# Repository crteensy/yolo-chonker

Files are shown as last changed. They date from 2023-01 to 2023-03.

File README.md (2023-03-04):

# yolo-chonker

## if you are a betaflight dev and received an assembled board from crteensy

There is a branch with the "as-built" state that you received: https://github.com/crteensy/yolo-chonker/tree/as-built-20230303

It includes a description of minor mistakes and errors, and what paste (high temp, low temp) was used where.

## What this is

betaflight developer FC for the H735

The layout has 6 layers, and the decoupling is designed for oshpark's 6-layer stackup (see oshpark_6L_stackup.png)

- Format: 30x30 hole distance
- Battery voltage range: 2-6S
- 5V DCDC: LMR33620CRNXT
- 3V3: TPS62824
- Separate DCDC for HD out; LMR33620CRNXT set for 10V or 5V, configured with a solder jumper
- MCU: STM32H735
- peripherals that can be connected to the MCU with solder jumpers:
  - IMU: ICM-20602 and BMI270; dual gyro is possible
  - Flash: S25FL064L
  - Baro: DPS310
  - LEDs:
    - voltage rails LEDs: HD DCDC (5/10 V), 5V, 3V3
    - two standard LEDs for the FC
    - WS2812B including an output pad to attach more
  - battery voltage sensing
- SWD pads
- no analog OSD
- no HD connector

CC-BY-SA-4.0
https://creativecommons.org/licenses/by-sa/4.0/legalcode

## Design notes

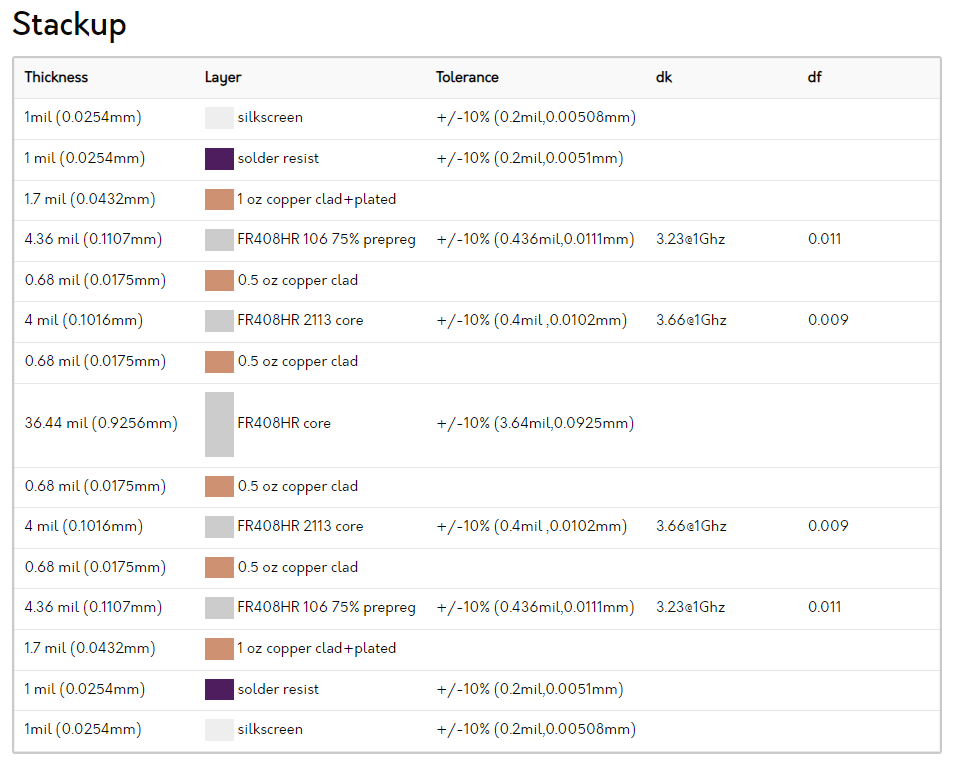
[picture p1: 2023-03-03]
oshpark_6L_stackup.png

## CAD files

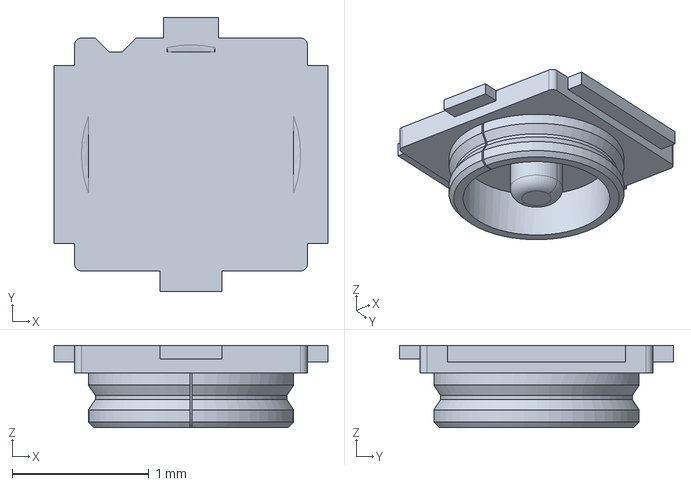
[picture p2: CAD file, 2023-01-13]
3D/A-4JA.stp
2.00 x 2.00 x 0.6 mm

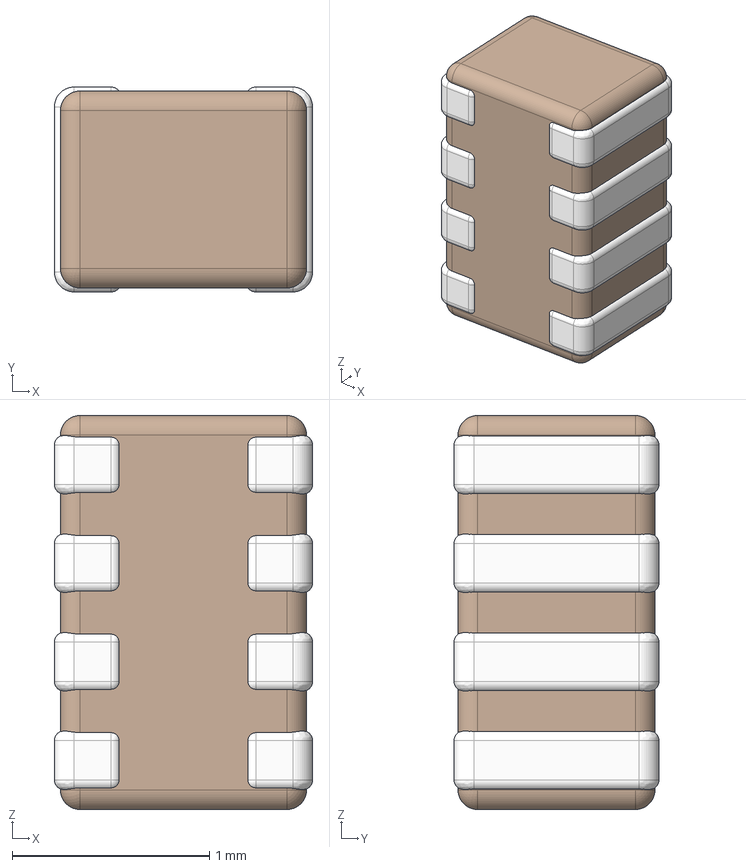
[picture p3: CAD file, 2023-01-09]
3D/idc.stp
1.31 x 1.04 x 2.00 mm

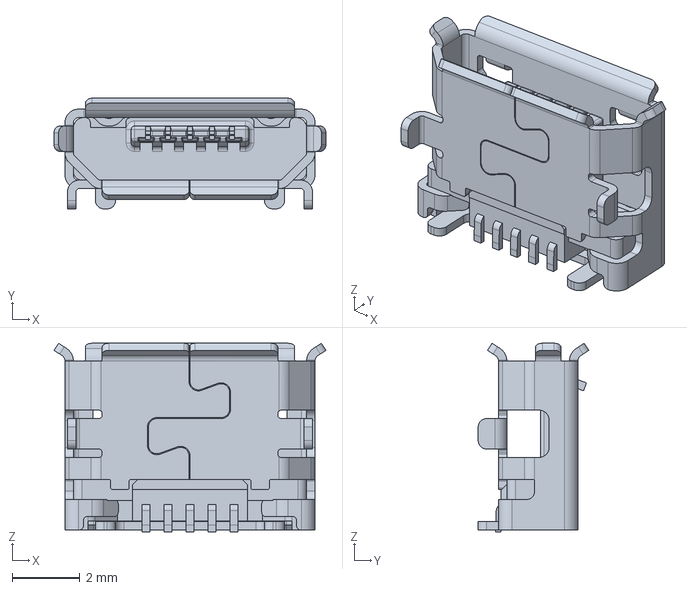
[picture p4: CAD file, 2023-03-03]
3D/10118194c.stp
8.05 x 3.27 x 5.58 mm

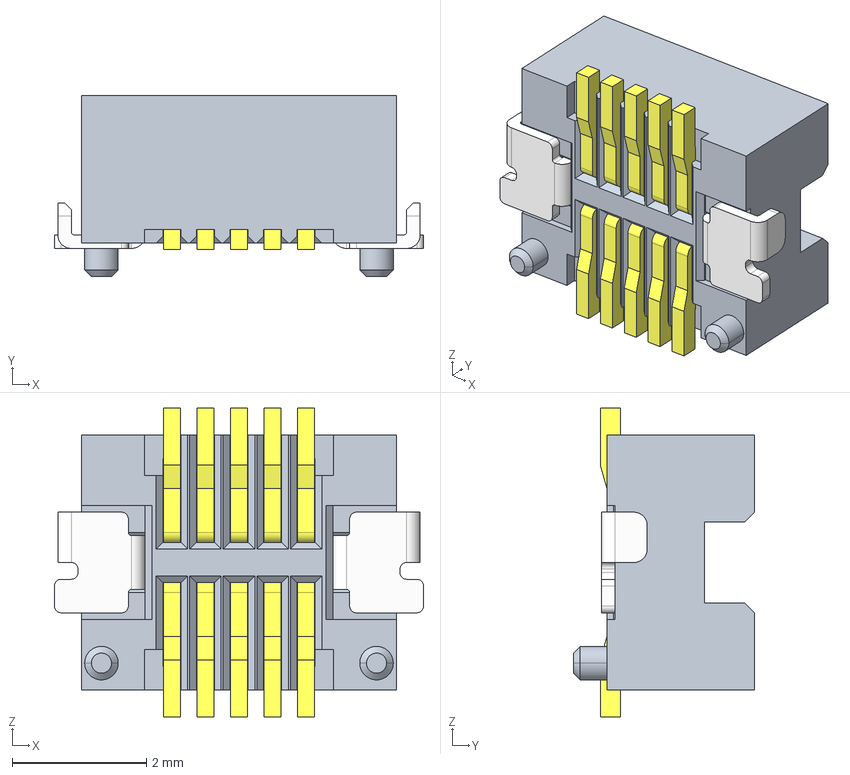
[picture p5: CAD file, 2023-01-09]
3D/10132797-011100LF.stp
5.50 x 2.70 x 4.60 mm
30H-10PIN-F-H
30H-F-TERMINAL x 5

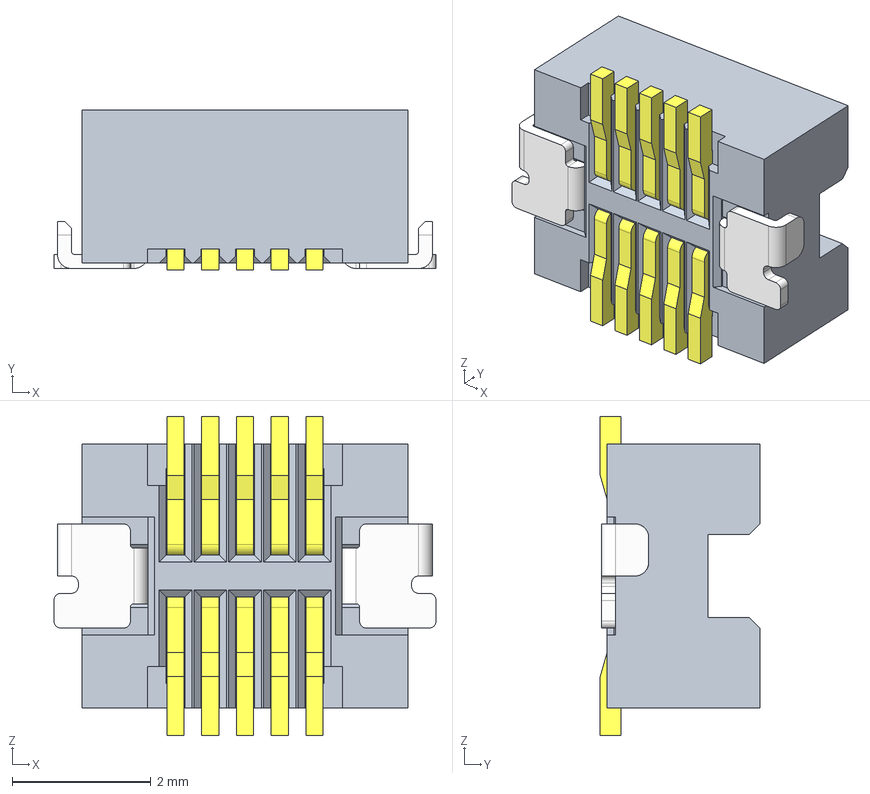
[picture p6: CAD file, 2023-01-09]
3D/10132797-011110LF.stp
5.50 x 2.30 x 4.60 mm
30H-10PIN-F-H
30H-F-TERMINAL x 5

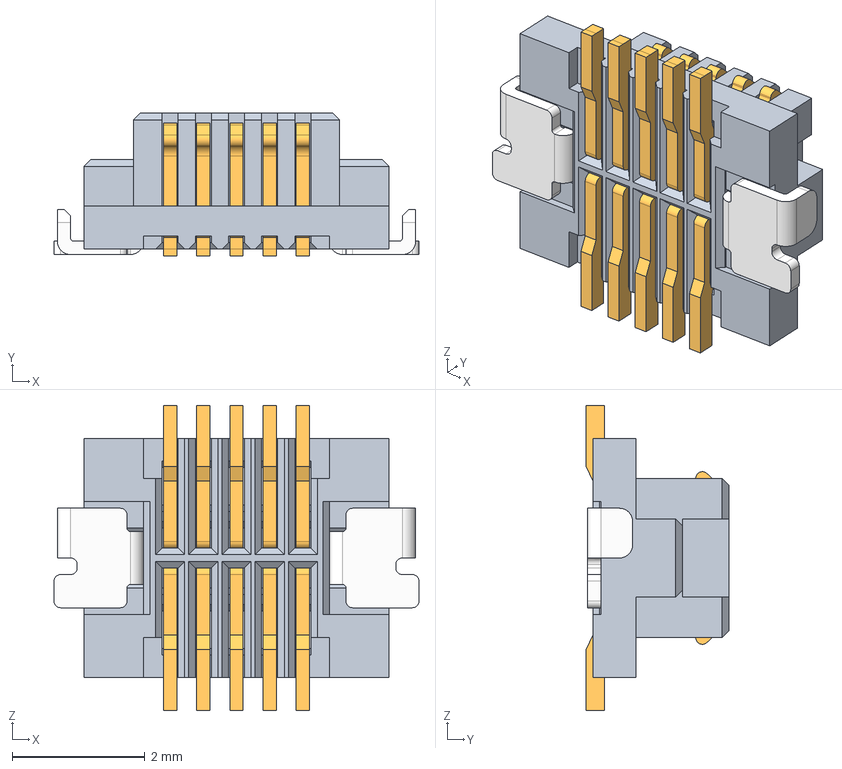
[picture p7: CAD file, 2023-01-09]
3D/10132798-011110LF.stp
5.50 x 2.15 x 4.60 mm
30H-10PIN-M-H
30H-M-TERMINAL x 5

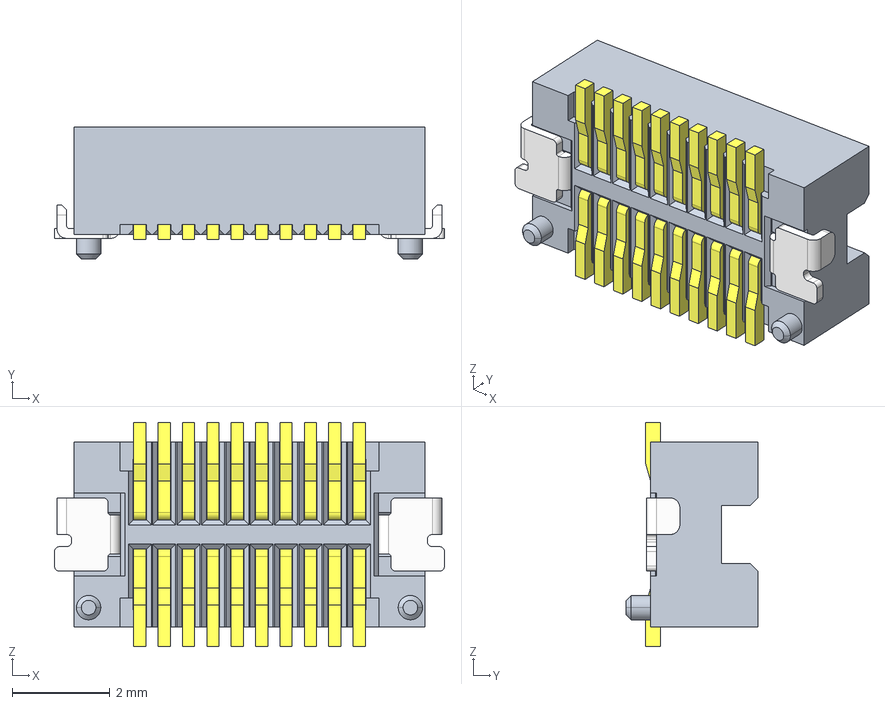
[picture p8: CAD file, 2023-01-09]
3D/10132797-021100LF.stp
8.00 x 2.70 x 4.60 mm
30H-20PIN-F-H
30H-F-TERMINAL x 10

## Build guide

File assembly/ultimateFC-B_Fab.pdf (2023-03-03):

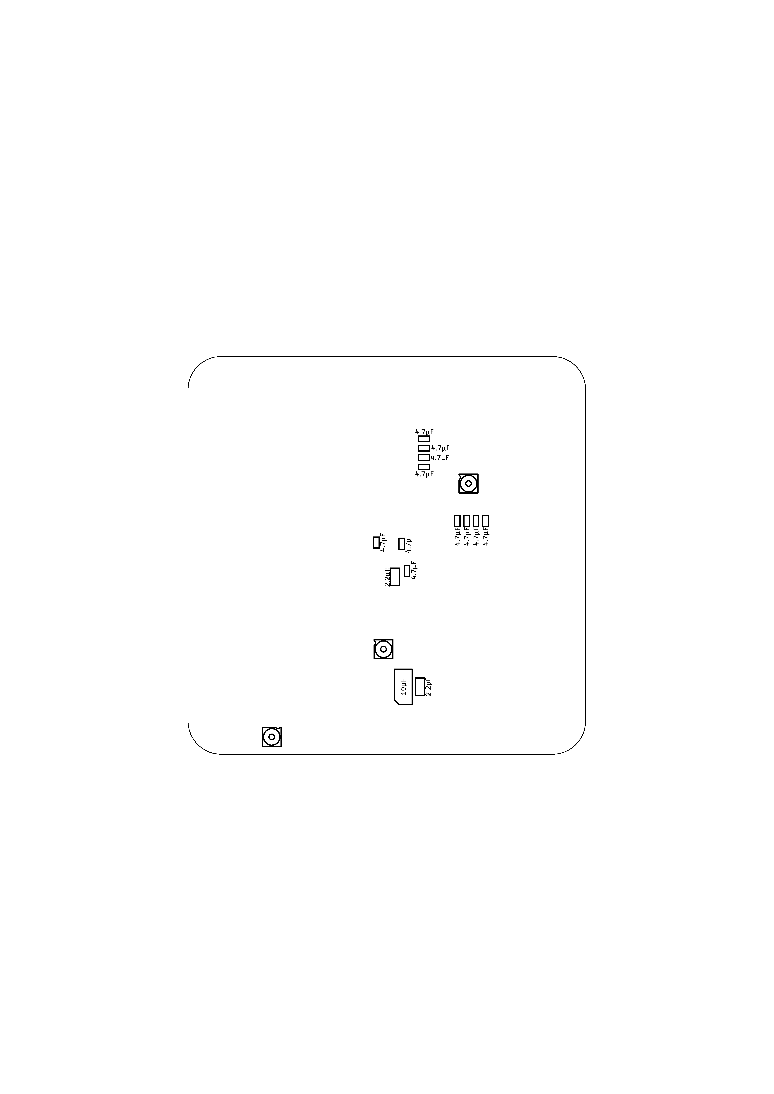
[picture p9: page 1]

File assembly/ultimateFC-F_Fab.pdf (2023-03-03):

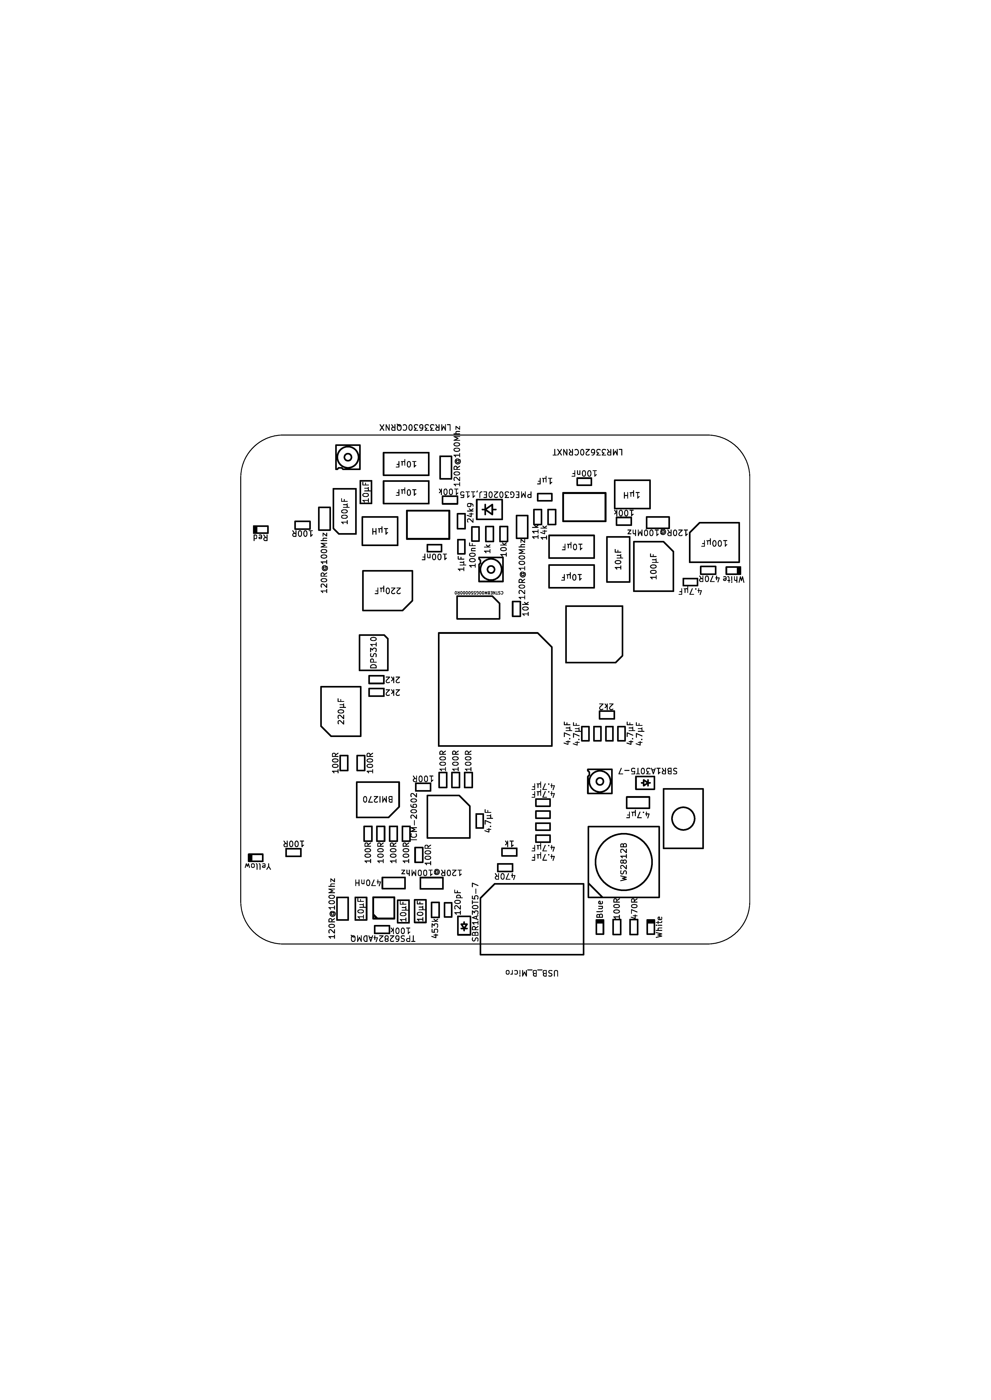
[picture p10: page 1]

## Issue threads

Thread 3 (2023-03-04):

update gerbers

crteensy, 2023-03-04:
minor layout fixes require re-generation of gerbers.
one GND pad had no label, this was added and has to be subtracted from bottom copper before generating the gerber file.

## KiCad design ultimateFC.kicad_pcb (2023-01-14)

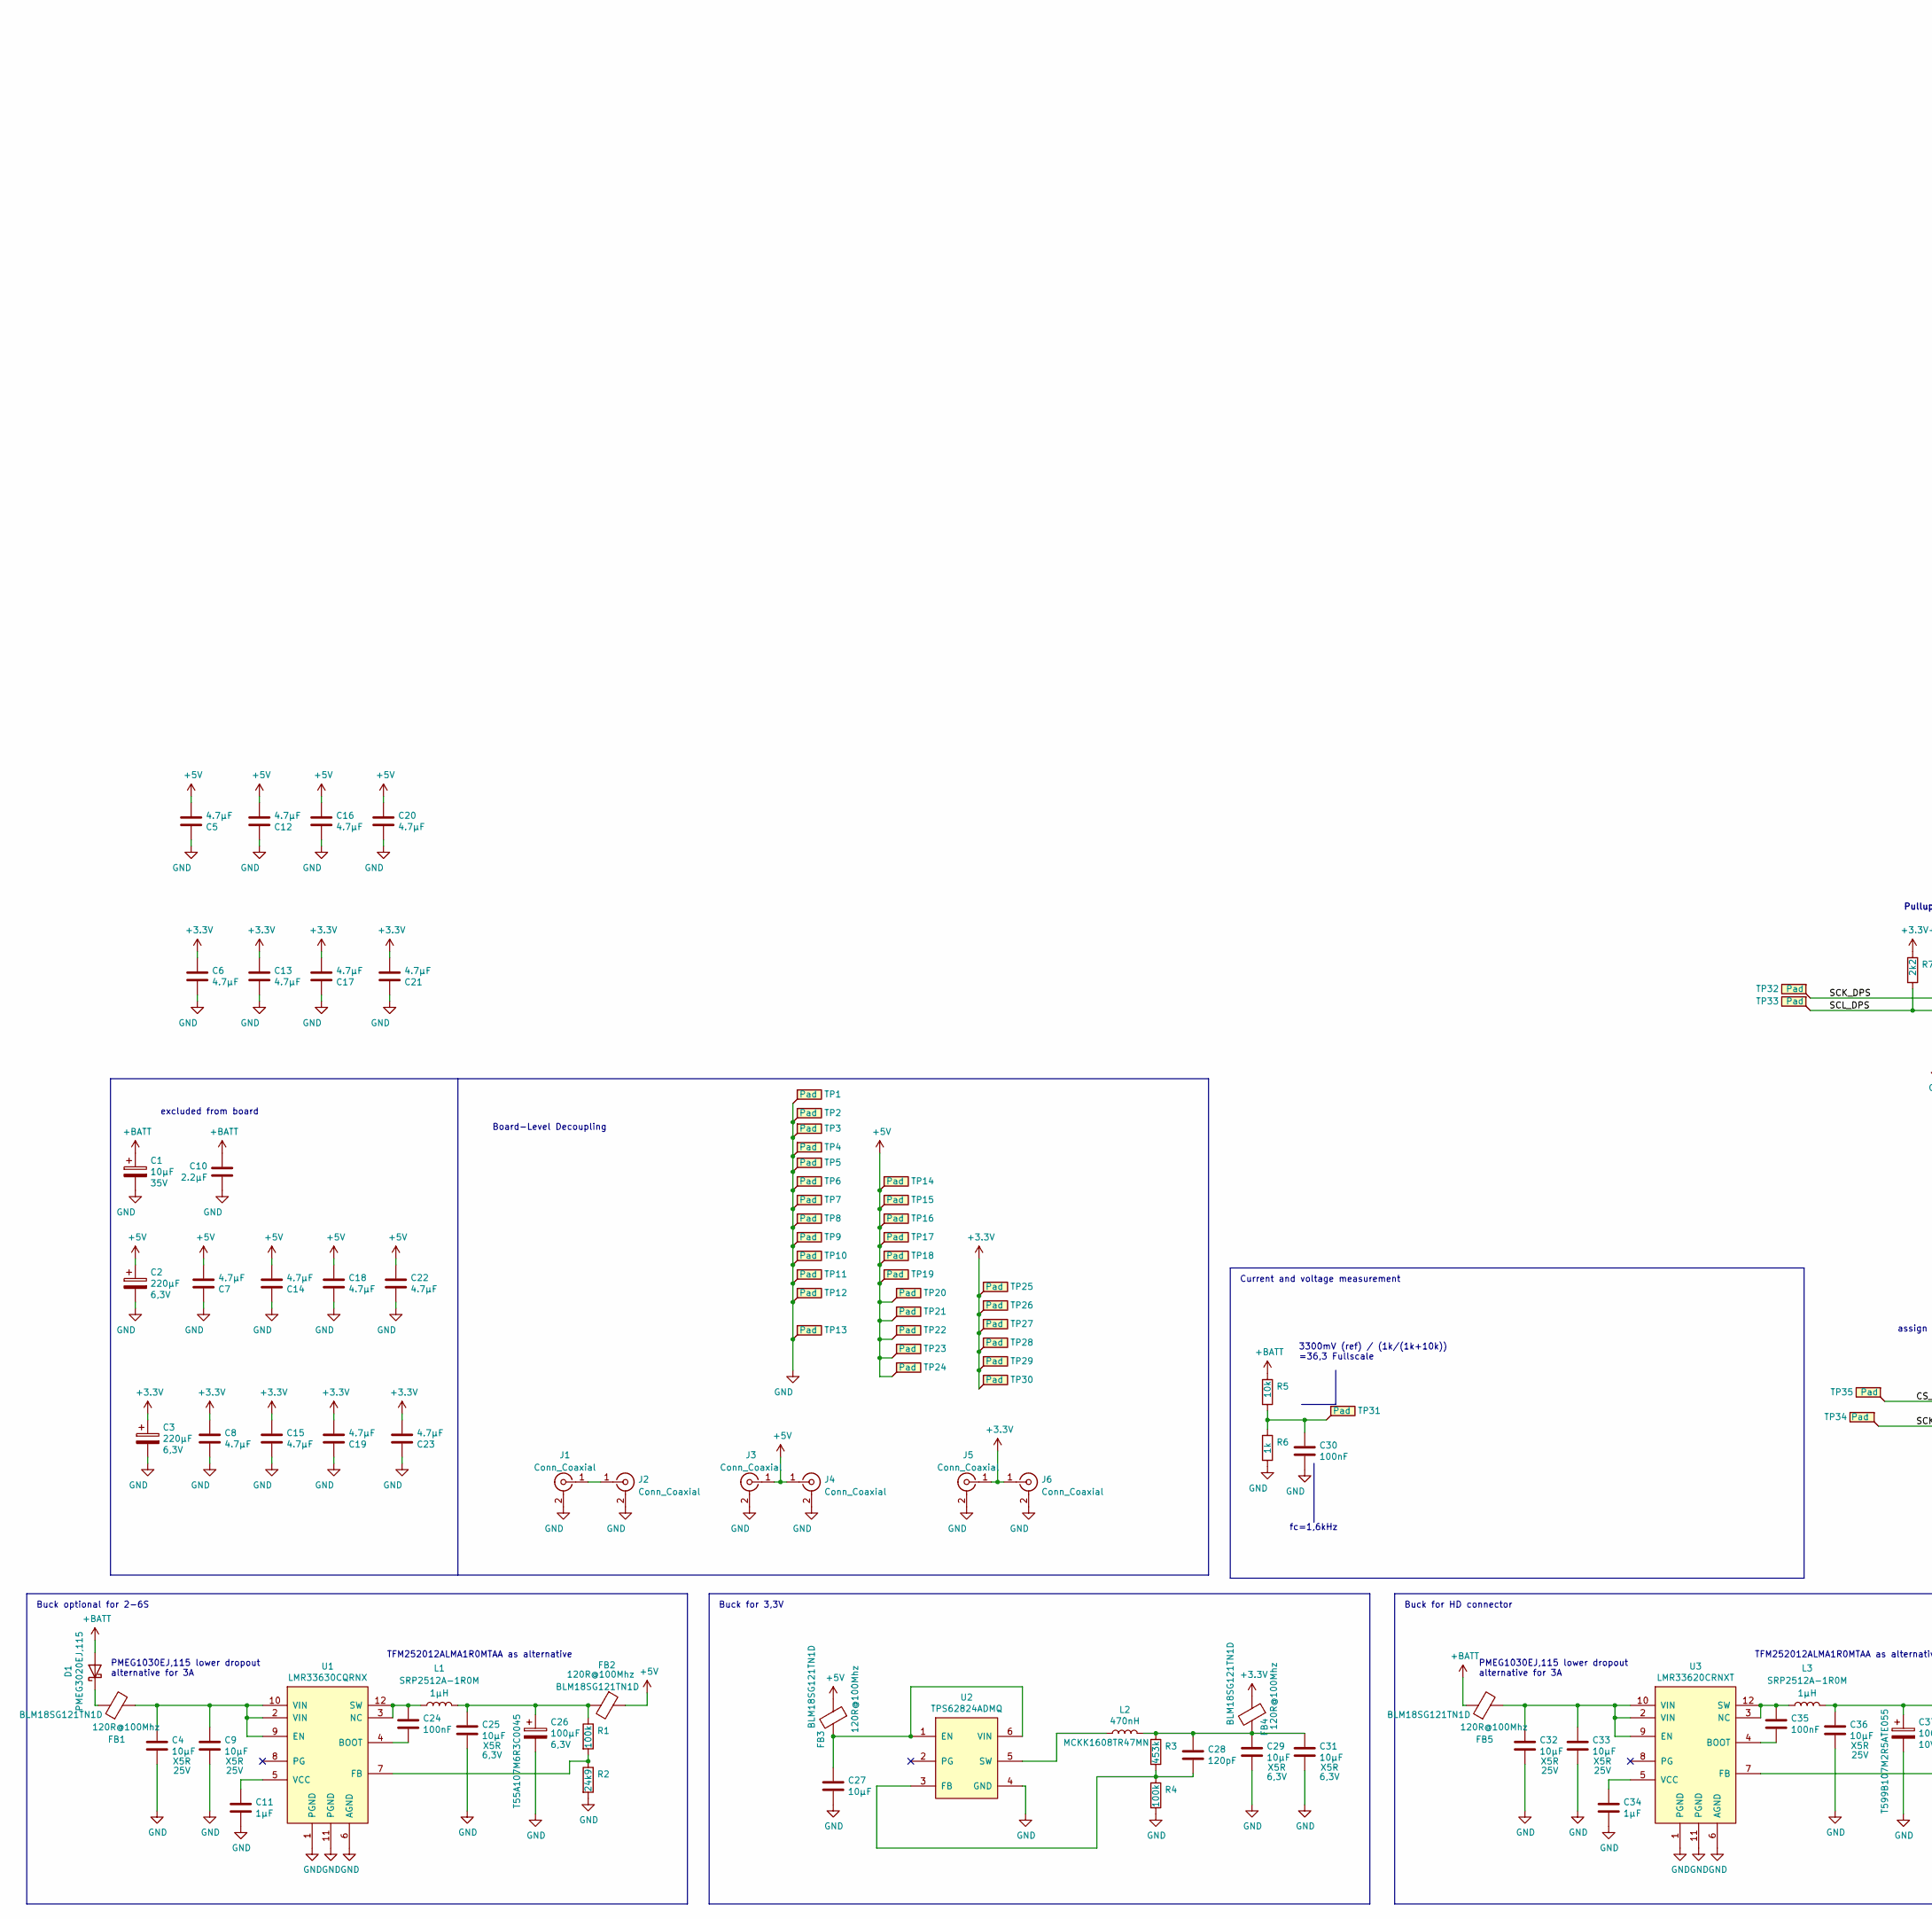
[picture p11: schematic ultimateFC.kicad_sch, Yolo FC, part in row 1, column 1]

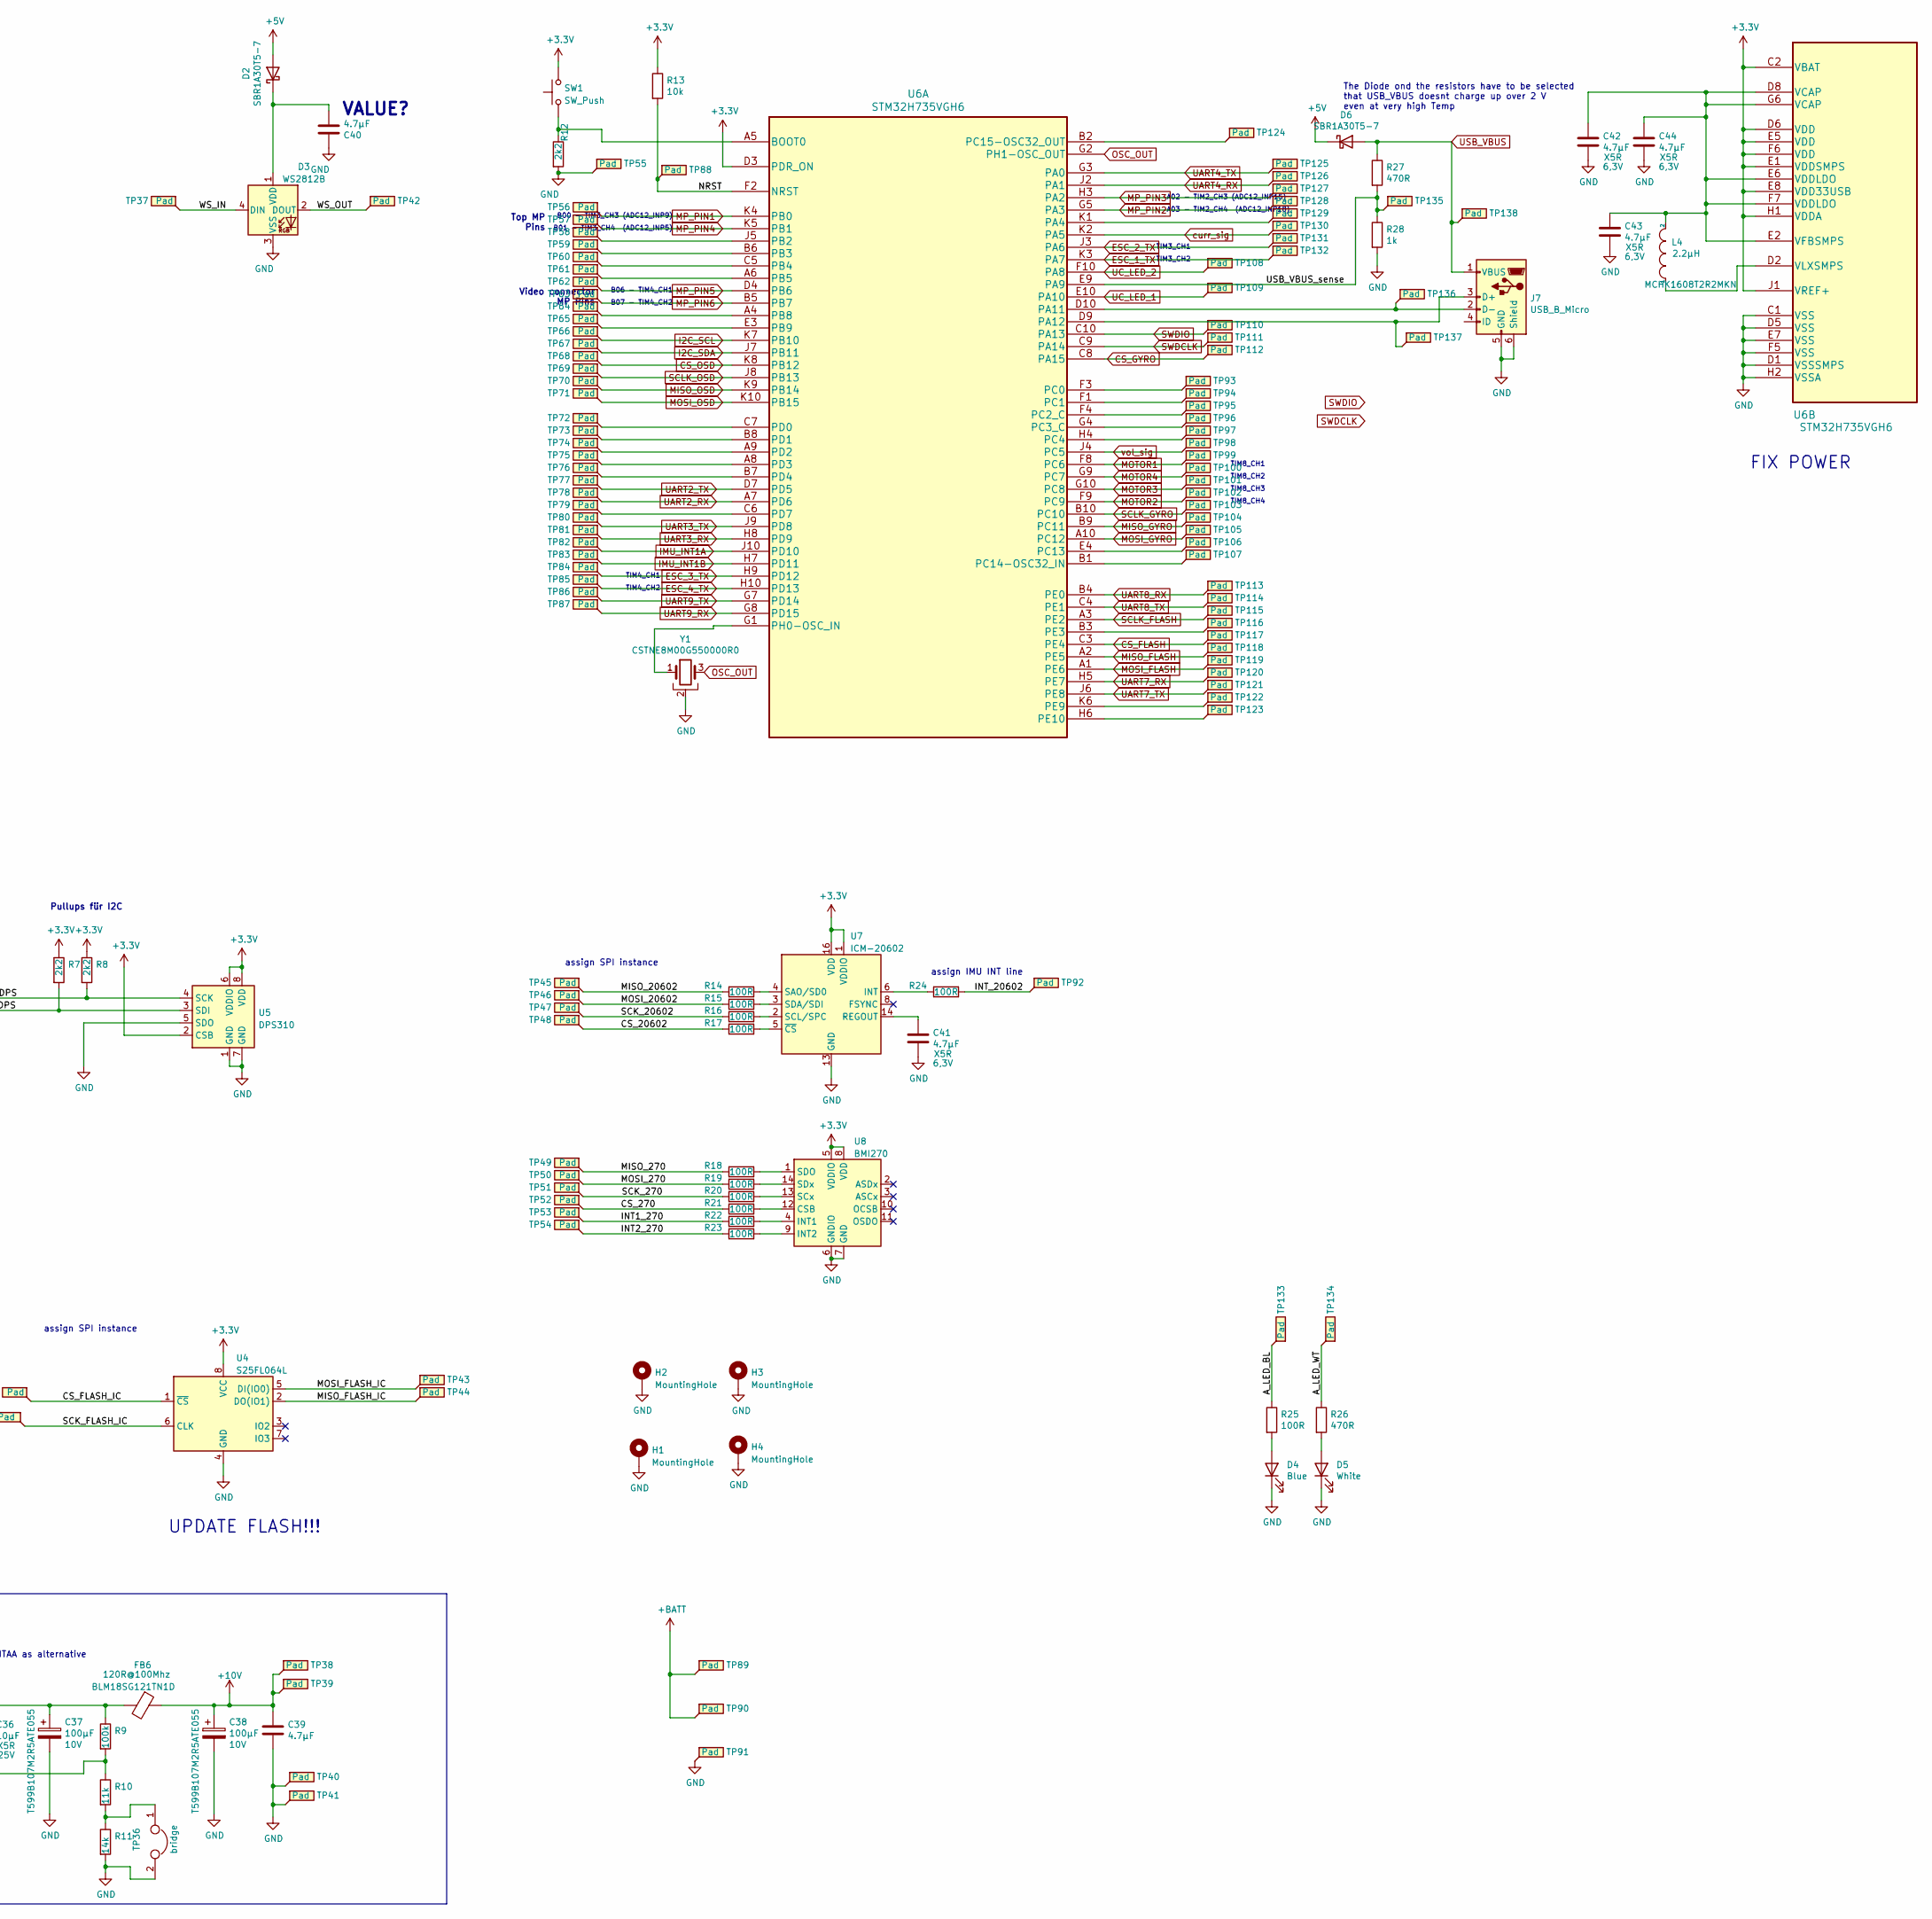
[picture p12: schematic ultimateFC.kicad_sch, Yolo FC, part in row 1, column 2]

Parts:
C1: 10µF; CP_EIA-3216-18_Kemet-A
C2, C3: 220µF; CP_EIA-3528-15_AVX-H
C4, C9, C32, C33, C36: 10µF; C_1206_3216Metric
C5, C6, C7, C8, C12, C13, C14, C15, C16, C17, C18, C19, C20, C21, C22, C23, C39, C41, C42, C43, C44: 4.7µF; C_0402_1005Metric
C10: 2.2µF; C_0603_1608Metric
C11, C34: 1µF; C_0402_1005Metric
C24, C30, C35: 100nF; C_0402_1005Metric
C25, C27, C29, C31: 10µF; C_0603_1608Metric
C26: 100µF; CP_EIA-3216-10_Kemet-I
C28: 120pF; C_0402_1005Metric
C37, C38: 100µF; CP_EIA-3528-12_Kemet-T
C40: 4.7µF; C_0603_1608Metric
D1: PMEG3020EJ,115; D_SOD-323
D2, D6: SBR1A30T5-7; D_SOD-523
D3: WS2812B; LED_WS2812B_PLCC4_5.0x5.0mm_P3.2mm
D4: Blue; LED_0402_1005Metric
D5: White; LED_0402_1005Metric
FB1, FB2, FB3, FB4, FB5, FB6: 120R@100Mhz; L_0603_1608Metric
H1, H2, H3, H4: MountingHole; MountingHole_3.2mm_M3_DIN965_Pad
J1, J2, J3, J4, J5, J6: Conn_Coaxial; Amphenol_RF_A-4JA
J7: USB_B_Micro; USB_Micro-B_Amphenol_10118194_Horizontal
L1, L3: 1µH; L_Wuerth_MAPI-2506
L2: 470nH; L_0603_1608Metric
L4: 2.2µH; L_0603_1608Metric
R1, R4, R9: 100k; R_0402_1005Metric
R2: 24k9; R_0402_1005Metric
R3: 453k; R_0402_1005Metric
R5, R13: 10k; R_0402_1005Metric
R6, R28: 1k; R_0402_1005Metric
R7, R8, R12: 2k2; R_0402_1005Metric
R10: 11k; R_0402_1005Metric
R11: 14k; R_0402_1005Metric
R14, R15, R16, R17, R18, R19, R20, R21, R22, R23, R24, R25: 100R; R_0402_1005Metric
R26, R27: 470R; R_0402_1005Metric
SW1: SW_Push; SW_Push_1P1T-SH_NO_CK_KMR2xxG
TP1, TP2, TP3, TP4, TP5, TP6, TP7, TP8, TP9, TP10, TP11, TP12, TP13, TP14, TP15, TP16, TP17, TP18, TP19, TP20, TP21, TP22, TP23, TP24, TP26, TP27, TP28, TP29, TP30, TP38, TP39, TP40, TP41, TP42, TP56, TP57, TP58, TP59, TP60, TP61, TP62, TP63, TP64, TP65, TP66, TP67, TP68, TP69, TP70, TP71, TP72, TP73, TP74, TP75, TP76, TP77, TP78, TP79, TP80, TP81, TP82, TP83, TP84, TP85, TP86, TP87, TP89, TP93, TP94, TP95, TP96, TP97, TP98, TP99, TP100, TP101, TP102, TP103, TP104, TP105, TP106, TP107, TP108, TP109, TP112, TP113, TP114, TP115, TP116, TP117, TP118, TP119, TP120, TP121, TP122, TP123, TP124, TP125, TP126, TP127, TP128, TP129, TP130, TP131, TP132: Pad; chonker_TestPoint_Pad_1.5x2.0mm
TP25, TP55, TP88, TP110, TP111: Pad; chonker_swd_pad
TP31, TP32, TP33, TP34, TP35, TP37, TP43, TP44, TP45, TP46, TP47, TP48, TP49, TP50, TP51, TP52, TP53, TP54, TP92, TP133, TP134, TP135, TP136, TP137, TP138: Pad; chonker_TestPoint_Pad_1.5x1.5mm
TP36: bridge; solderbridge_tiny
TP90, TP91: Pad; TestPoint_Pad_3.0x3.0mm
U1: LMR33630CQRNX; Texas_RNX0012B
U2: TPS62824ADMQ; VSON_HR6
U3: LMR33620CRNXT; Texas_RNX0012B
U4: S25FL064L; WSON-8_4x4mm_P0.8mm
U5: DPS310; Bosch_LGA-8_2x2.5mm_P0.65mm_ClockwisePinNumbering
U6: STM32H735VGH6; TFBGA-100_8x8mm_Layout10x10_P0.8mm
U7: ICM-20602; LGA-16_3x3mm_P0.5mm_LayoutBorder3x5y
U8: BMI270; Bosch_LGA-14_3x2.5mm_P0.5mm
Y1: CSTNE8M00G550000R0; Resonator_SMD_muRata_CSTxExxV-3Pin_3.0x1.1mm

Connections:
+3V3: C3.1, C6.1, C8.1, C13.1, C15.1, C17.2, C19.2, C21.2, C23.2, FB4.1, J5.1 (In), J6.1 (In), R7.1, R8.1, R13.1, SW1.2, TP25.1, TP26.1, TP27.1, TP28.1, TP29.1, TP30.1, U4.8 (VCC), U5.2 (CSB), U5.6 (VDDIO), U5.8 (VDD), U6.C2 (VBAT), U6.D3 (PDR_ON), U6.D6 (VDD), U6.E1 (VDDSMPS), U6.E5 (VDD), U6.E8 (VDD33USB), U6.F6 (VDD), U6.H1 (VDDA), U6.J1 (VREF+), U7.1 (VDDIO), U7.16 (VDD), U8.5 (VDDIO), U8.8 (VDD)
+5V: C2.1, C5.2, C7.2, C12.2, C14.2, C16.1, C18.1, C20.1, C22.1, D2.2 (A), D6.1 (K), FB2.1, FB3.1, J3.1 (In), J4.1 (In), TP14.1, TP15.1, TP16.1, TP17.1, TP18.1, TP19.1, TP20.1, TP21.1, TP22.1, TP23.1, TP24.1
+10V: C38.1, C39.1, FB6.1, TP38.1, TP39.1
+BATT: C1.1, C10.1, D1.2 (A), FB5.1, R5.1, TP89.1, TP90.1
/A_LED_BL: R25.1, TP133.1
/A_LED_WT: R26.1, TP134.1
/CS_270: R21.1, TP52.1
/CS_20602: R17.1, TP48.1
/CS_FLASH_IC: TP35.1, U4.1 (~CS)
/INT1_270: R22.1, TP53.1
/INT2_270: R23.1, TP54.1
/INT_20602: R24.2, TP92.1
/MISO_270: R18.1, TP49.1
/MISO_20602: R14.1, TP45.1
/MISO_FLASH_IC: TP44.1, U4.2 (DO(IO1))
/MOSI_270: R19.1, TP50.1
/MOSI_20602: R15.1, TP46.1
/MOSI_FLASH_IC: TP43.1, U4.5 (DI(IO0))
/NRST: R13.2, TP88.1, U6.F2 (NRST)
/SCK_270: R20.1, TP51.1
/SCK_20602: R16.1, TP47.1
/SCK_DPS: R8.2, TP32.1, U5.4 (SCK)
/SCK_FLASH_IC: TP34.1, U4.6 (CLK)
/SCL_DPS: R7.2, TP33.1, U5.3 (SDI)
/USB_VBUS_sense: R27.2, R28.1, TP135.1, U6.E9 (PA9)
/WS_IN: D3.4 (DIN), TP37.1
/WS_OUT: D3.2 (DOUT), TP42.1
CS_FLASH: TP117.1, U6.C3 (PE4)
CS_GYRO: TP112.1, U6.C8 (PA15)
CS_OSD: TP68.1, U6.K8 (PB12)
ESC_1_TX: TP132.1, U6.K3 (PA7)
ESC_2_TX: TP131.1, U6.J3 (PA6)
ESC_3_TX: TP84.1, U6.H9 (PD12)
ESC_4_TX: TP85.1, U6.H10 (PD13)
GND: C1.2, C2.2, C3.2, C4.2, C5.1, C6.2, C7.1, C8.2, C9.2, C10.2, C11.2, C12.1, C13.2, C14.1, C15.2, C16.2, C17.1, C18.2, C19.1, C20.2, C21.1, C22.2, C23.1, C25.2, C26.2, C27.2, C29.2, C30.2, C31.2, C32.2, C33.2, C34.2, C36.2, C37.2, C38.2, C39.2, C40.1, C41.2, C42.2, C43.2, C44.2, D3.3 (VSS), D4.1 (K), D5.1 (K), H1.1, H2.1, H3.1, H4.1, J1.2 (Ext), J2.2 (Ext), J3.2 (Ext), J4.2 (Ext), J5.2 (Ext), J6.2 (Ext), J7.5 (GND), J7.6 (Shield), R2.2, R4.2, R6.2, R11.2, R12.2, R28.2, TP1.1, TP2.1, TP3.1, TP4.1, TP5.1, TP6.1, TP7.1, TP8.1, TP9.1, TP10.1, TP11.1, TP12.1, TP13.1, TP36.2, TP40.1, TP41.1, TP55.1, TP91.1, U1.1 (PGND), U1.6 (AGND), U1.11 (PGND), U2.4 (GND), U3.1 (PGND), U3.6 (AGND), U3.11 (PGND), U4.4 (GND), U5.1 (GND), U5.5 (SDO), U5.7 (GND), U6.C1 (VSS), U6.D1 (VSSSMPS), U6.D5 (VSS), U6.E7 (VSS), U6.F5 (VSS), U6.H2 (VSSA), U7.9 (GND), U7.10 (GND), U7.11 (GND), U7.12 (GND), U7.13 (GND), U7.15 (GND), U8.6 (GNDIO), U8.7 (GND), Y1.2
I2C_SCL: TP66.1, U6.K7 (PB10)
I2C_SDA: TP67.1, U6.J7 (PB11)
IMU_INT1A: TP82.1, U6.J10 (PD10)
IMU_INT1B: TP83.1, U6.H7 (PD11)
MISO_FLASH: TP118.1, U6.A2 (PE5)
MISO_GYRO: TP104.1, U6.B9 (PC11)
MISO_OSD: TP70.1, U6.K9 (PB14)
MOSI_FLASH: TP119.1, U6.A1 (PE6)
MOSI_GYRO: TP105.1, U6.A10 (PC12)
MOSI_OSD: TP71.1, U6.K10 (PB15)
MOTOR1: TP99.1, U6.F8 (PC6)
MOTOR2: TP102.1, U6.F9 (PC9)
MOTOR3: TP101.1, U6.G10 (PC8)
MOTOR4: TP100.1, U6.G9 (PC7)
MP_PIN1: TP56.1, U6.K4 (PB0)
MP_PIN2: TP128.1, U6.G5 (PA3)
MP_PIN3: TP127.1, U6.H3 (PA2)
MP_PIN4: TP57.1, U6.K5 (PB1)
MP_PIN5: TP62.1, U6.D4 (PB6)
MP_PIN6: TP63.1, U6.B5 (PB7)
unnamed: C4.1, C9.1, FB1.2, U1.2 (VIN), U1.9 (EN), U1.10 (VIN)
unnamed: C11.1, U1.5 (VCC)
unnamed: C24.1, L1.1, U1.3 (NC), U1.12 (SW)
unnamed: C24.2, U1.4 (BOOT)
unnamed: C25.1, C26.1, FB2.2, L1.2, R1.1
unnamed: C27.1, FB3.2, U2.1 (EN), U2.6 (VIN)
unnamed: C28.1, C29.1, C31.1, FB4.2, L2.2, R3.1
unnamed: C28.2, R3.2, R4.1, U2.3 (FB)
unnamed: C30.1, R5.2, R6.1, TP31.1
unnamed: C32.1, C33.1, FB5.2, U3.2 (VIN), U3.9 (EN), U3.10 (VIN)
unnamed: C34.1, U3.5 (VCC)
unnamed: C35.1, L3.1, U3.3 (NC), U3.12 (SW)
unnamed: C35.2, U3.4 (BOOT)
unnamed: C36.1, C37.1, FB6.2, L3.2, R9.1
unnamed: C40.2, D2.1 (K), D3.1 (VDD)
unnamed: C41.1, U7.14 (REGOUT)
unnamed: C42.1, C43.1, C44.1, L4.2, U6.D8 (VCAP), U6.E2 (VFBSMPS), U6.E6 (VDDLDO), U6.F7 (VDDLDO), U6.G6 (VCAP)
unnamed: D1.1 (K), FB1.1
unnamed: D4.2 (A), R25.2
unnamed: D5.2 (A), R26.2
unnamed: J1.1 (In), J2.1 (In)
unnamed: J7.2 (D-), TP136.1, U6.D10 (PA11)
unnamed: J7.3 (D+), TP137.1, U6.D9 (PA12)
unnamed: L2.1, U2.5 (SW)
unnamed: L4.1, U6.D2 (VLXSMPS)
unnamed: R1.2, R2.1, U1.7 (FB)
unnamed: R9.2, R10.1, U3.7 (FB)
unnamed: R10.2, R11.1, TP36.1
unnamed: R12.1, SW1.1, U6.A5 (BOOT0)
unnamed: R14.2, U7.4 (SAO/SD0)
unnamed: R15.2, U7.3 (SDA/SDI)
unnamed: R16.2, U7.2 (SCL/SPC)
unnamed: R17.2, U7.5 (~CS)
unnamed: R18.2, U8.1 (SDO)
unnamed: R19.2, U8.14 (SDx)
unnamed: R20.2, U8.13 (SCx)
unnamed: R21.2, U8.12 (CSB)
unnamed: R22.2, U8.4 (INT1)
unnamed: R23.2, U8.9 (INT2)
unnamed: R24.1, U7.6 (INT)
unnamed: TP58.1, U6.J5 (PB2)
unnamed: TP59.1, U6.B6 (PB3)
unnamed: TP60.1, U6.C5 (PB4)
unnamed: TP61.1, U6.A6 (PB5)
unnamed: TP64.1, U6.A4 (PB8)
unnamed: TP65.1, U6.E3 (PB9)
unnamed: TP72.1, U6.C7 (PD0)
unnamed: TP73.1, U6.B8 (PD1)
unnamed: TP74.1, U6.A9 (PD2)
unnamed: TP75.1, U6.A8 (PD3)
unnamed: TP76.1, U6.B7 (PD4)
unnamed: TP79.1, U6.C6 (PD7)
unnamed: TP93.1, U6.F3 (PC0)
unnamed: TP94.1, U6.F1 (PC1)
unnamed: TP95.1, U6.F4 (PC2_C)
unnamed: TP96.1, U6.G4 (PC3_C)
unnamed: TP97.1, U6.H4 (PC4)
unnamed: TP106.1, U6.E4 (PC13)
unnamed: TP107.1, U6.B1 (PC14-OSC32_IN)
unnamed: TP116.1, U6.B3 (PE3)
unnamed: TP122.1, U6.K6 (PE9)
unnamed: TP123.1, U6.H6 (PE10)
unnamed: TP124.1, U6.B2 (PC15-OSC32_OUT)
unnamed: TP129.1, U6.K1 (PA4)
unnamed: U6.G1 (PH0-OSC_IN), Y1.1
OSC_OUT: U6.G2 (PH1-OSC_OUT), Y1.3
SCLK_FLASH: TP115.1, U6.A3 (PE2)
SCLK_GYRO: TP103.1, U6.B10 (PC10)
SCLK_OSD: TP69.1, U6.J8 (PB13)
SWDCLK: TP111.1, U6.C9 (PA14)
SWDIO: TP110.1, U6.C10 (PA13)
UART2_RX: TP78.1, U6.A7 (PD6)
UART2_TX: TP77.1, U6.D7 (PD5)
UART3_RX: TP81.1, U6.H8 (PD9)
UART3_TX: TP80.1, U6.J9 (PD8)
UART4_RX: TP126.1, U6.J2 (PA1)
UART4_TX: TP125.1, U6.G3 (PA0)
UART7_RX: TP120.1, U6.H5 (PE7)
UART7_TX: TP121.1, U6.J6 (PE8)
UART8_RX: TP113.1, U6.B4 (PE0)
UART8_TX: TP114.1, U6.C4 (PE1)
UART9_RX: TP87.1, U6.G8 (PD15)
UART9_TX: TP86.1, U6.G7 (PD14)
UC_LED_1: TP109.1, U6.E10 (PA10)
UC_LED_2: TP108.1, U6.F10 (PA8)
USB_VBUS: D6.2 (A), J7.1 (VBUS), R27.1, TP138.1
curr_sig: TP130.1, U6.K2 (PA5)
vol_sig: TP98.1, U6.J4 (PC5)

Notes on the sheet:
Board-Level Decoupling
TIM8_CH2
B01 - TIM3_CH4 (ADC12_INP5)
TFM252012ALMA1R0MTAA as alternative
TIM8_CH4
B00 - TIM3_CH3 (ADC12_INP9)
TIM4_CH1
UPDATE FLASH!!!
Buck for 3,3V
Top MP Pins
A03 - TIM2_CH4 (ADC12_INP18)
TIM8_CH1
TIM8_CH3
TIM3_CH1
excluded from board
FIX POWER
assign SPI instance
Buck for HD connector
B07 - TIM4_CH2
Video connector MP Pins
PMEG1030EJ,115 lower dropout alternative for 3A
3300mV (ref) / (1k/(1k+10k)) =36,3 Fullscale
VALUE?
Current and voltage measurement
assign IMU INT line
Pullups für I2C
TIM3_CH2
fc=1,6kHz
TIM4_CH2
B06 - TIM4_CH1
Buck optional for 2-6S
A02 - TIM2_CH3 (ADC12_INP15)
The Diode ond the resistors have to be selected that USB_VBUS doesnt charge up over 2 V even at very high Temp

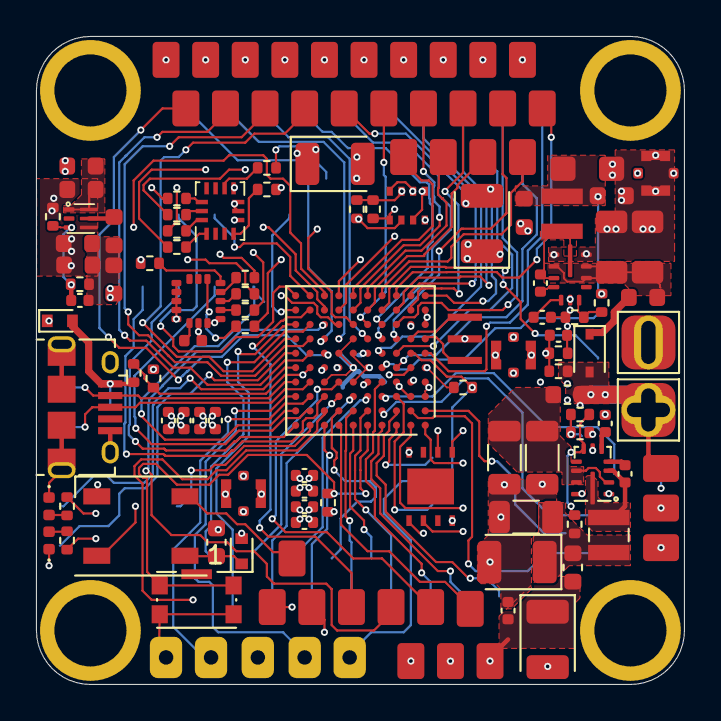
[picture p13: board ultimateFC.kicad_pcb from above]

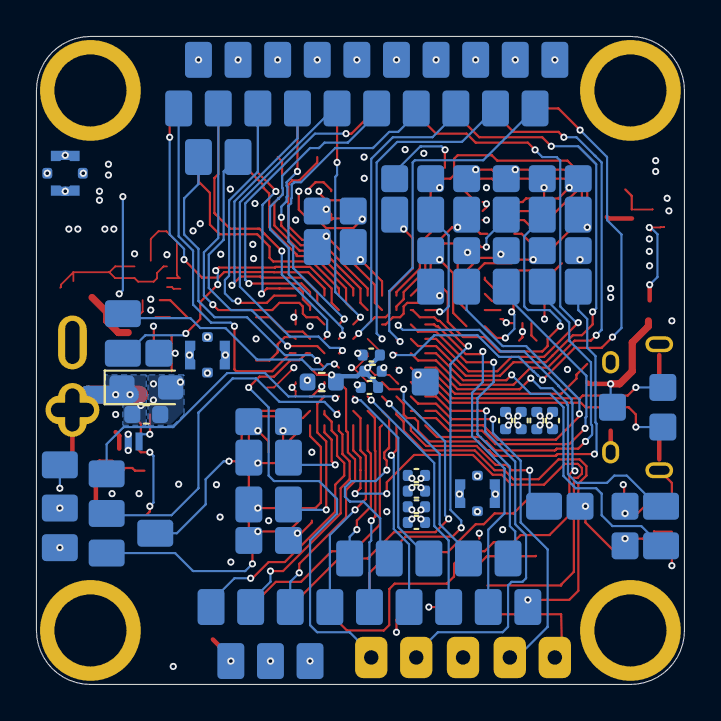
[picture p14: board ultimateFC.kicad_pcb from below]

Board: 6 copper layers, 36.0 x 36.0 mm, 247 parts (115 on the bottom side), 143 nets.

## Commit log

2023-01-09 initial schematic and layout
    [10132797-011100LF.stp, 10132797-011110LF.stp, 10132797-021100LF.stp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]
2023-01-09 add HD DCDC
    [ultimateFC.kicad_pcb, ultimateFC.kicad_sch]
2023-01-09 board edge
    [ultimateFC.kicad_pcb]
2023-01-09 update pcb layer count
    [ultimateFC.kicad_pcb]
2023-01-09 update H7 Power symbol (!)
    [ultimateFC.kicad_sch]
2023-01-09 added PADs.... lots of PADs
    [ultimateFC.kicad_pcb, ultimateFC.kicad_sch]
2023-01-10 schematic and layout update
    [ultimateFC.kicad_pcb, ultimateFC.kicad_sch]
2023-01-11 add DCDC spreadsheet
    [DCDC.xlsx]
2023-01-11 more layout
    [ultimateFC.kicad_pcb, ultimateFC.kicad_sch]
2023-01-11 update layout
    [ultimateFC.kicad_pcb]
2023-01-12 layout update
    [ultimateFC.kicad_pcb, ultimateFC.kicad_sch]
2023-01-12 add WS2812, update layout
    [ultimateFC.kicad_pcb, ultimateFC.kicad_sch]
2023-01-13 MORE PADS!!!
    [ultimateFC.kicad_pcb, ultimateFC.kicad_sch]
2023-01-13 DCDC layouts
    [ultimateFC.kicad_pcb]
2023-01-13 layout tweaks
    [ultimateFC.kicad_pcb, ultimateFC.kicad_sch]
2023-01-13 add RF connectors
    [A-4JA.stp, ultimateFC.kicad_pcb, ultimateFC.kicad_sch]
2023-01-13 change pads, add coax datasheet
    [ultimateFC.kicad_pcb, ultimateFC.kicad_sch]
2023-01-14 Added Caps
    [ultimateFC.kicad_pcb, ultimateFC.kicad_sch]
2023-01-14 add caps
    [ultimateFC.kicad_pcb]
2023-01-14 tons of vias
    [ultimateFC.kicad_pcb]
2023-01-15 update layout, labels, silkscreen
    [ultimateFC.kicad_pcb, ultimateFC.kicad_sch]
2023-01-15 Canged to 125u pitch/width & added pad descriptions
2023-01-15 saved schematic
    [ultimateFC.kicad_sch]
2023-01-15 pad labeling and silkscreen
    [ultimateFC.kicad_sch]
2023-03-03 some minor changes
    [10118194c.stp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]
2023-03-03 add assembly pdfs
2023-03-03 add labeling error note in schematic
    [ultimateFC.kicad_sch]
2023-03-03 schematic: add vis-a-vis pad notes
    [ultimateFC.kicad_sch]
2023-03-03 add schematic pdf
2023-03-03 add license
    [ultimateFC.kicad_sch]
2023-03-04 add I2C cross jumper photo
2023-03-04 update as-built state schematic annotations low temp layer in layout
    [ultimateFC.kicad_sch]
2023-03-04 fix errors and mistakes, update schematic
    [ultimateFC.kicad_sch]
2023-03-25 minor layout tweaks
    [ultimateFC-B_Cu.gbr, ultimateFC-B_Mask.gbr, ultimateFC-B_Silkscreen.gbr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]
2023-03-25 minor schematic tweak
    [ultimateFC.kicad_sch]
2023-04-22 add JLC part numbers
    [ultimateFC.kicad_sch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]

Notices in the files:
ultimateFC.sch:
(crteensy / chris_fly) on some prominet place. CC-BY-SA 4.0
